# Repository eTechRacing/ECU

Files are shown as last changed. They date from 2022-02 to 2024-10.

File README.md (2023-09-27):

# SHIELD

ADCAN files moved to ADCAN-Legacy branch

_Pendent de publicar en angles

La shield ha de ser una placa versàtil i robusta que serveixi per implementar fàcilment elements comuns que comparteixen diverses plaques. L’avantatge d’implementar una shield és la de disposar d’una base coneguda, provada i fiable per, 
a partir d’ella, implementar qualsevol altre sistema que s’hagi d’incloure dins del cotxe.
Les funcionalitats de la placa shield passen, principalment, per una alimentació estable i constant i per un bus de comunicacions amplament validat i funcional. 
Tot això rodejant d’un microcontrolador molt consistent encarregat de l’adquisició, el processament i l’enviament de dades.

Requisits:
-Alimentació a 5 V i 3.3 V a partir de LV
-Comunicació via CAN1 i CAN2
-Connectors plug-and-play
-MCU potent (STM23)
-Documentació
-Reduir EMIs i soroll amb un bon disseny

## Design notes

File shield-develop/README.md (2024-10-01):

# SHIELD

ADCAN files moved to ADCAN-Legacy branch

_Pendent de publicar en angles

La shield ha de ser una placa versàtil i robusta que serveixi per implementar fàcilment elements comuns que comparteixen diverses plaques. L’avantatge d’implementar una shield és la de disposar d’una base coneguda, provada i fiable per, 
a partir d’ella, implementar qualsevol altre sistema que s’hagi d’incloure dins del cotxe.
Les funcionalitats de la placa shield passen, principalment, per una alimentació estable i constant i per un bus de comunicacions amplament validat i funcional. 
Tot això rodejant d’un microcontrolador molt consistent encarregat de l’adquisició, el processament i l’enviament de dades.

Requisits:
-Alimentació a 5 V i 3.3 V a partir de LV
-Comunicació via CAN1 i CAN2
-Connectors plug-and-play
-MCU potent (STM23)
-Documentació
-Reduir EMIs i soroll amb un bon disseny

El conntector entre la shield i la carrier és una de les parts fonamentals de la placa. La idea és que hi hagi connexió electrica i mecànica entre elles.
S'opta per un connector board-to-board tipus pin header (fabricant Würth) ja que dona la opció d'encaixar una placa sobre l'altre i, a mes, de disposar de totes les connexions
amb un connector senzill de posar i treure.

El microcontrolador és el més potent que s'ha pogut aconseguir per patrocinadors. Més concretament el STM32F777VI6T que compleix de sobres tots els requisits. De totes maneres,
pensant en el fet de que la shield sigui una placa amb futur, s'afageix una memoria EEPROM utilitzat el I2C número 4 del STM32.

Pel que fa la resta de la placa no hi ha cap complicació. S'implementa un USB_OTG amb un connector micro USB 2.0 per debug i visualització de dades per PC. Es fa servir el CAN
transceiver MCP2551 de microchip (fàcil d'aconseguir per samples) i unes proteccions i filtres a la linea CAN bastant estàndard. La resta dels pins del MCU van directament al
pin header excepte:
-VBAT: es col·loca un divisor de tensió rebaixant 30V a 3.3V. Això permet fer servir VBAT com una entrada analogica per medir la tensió que ofereix la LV.
-VBUS: es fa servir com a entrada digital per detectar si hi ha presencia d'USB.
-NRST: pin de reset del micocontrolador. Necessari per programar. Se li posa un botó per també poder fer reset manualment.
-Boot0: se li posa un switch per curtcircuitar a 3.3V o a GND. Això permetrà setejar al micro com a blank i poder carregar informació des del USB o programar més facilment.

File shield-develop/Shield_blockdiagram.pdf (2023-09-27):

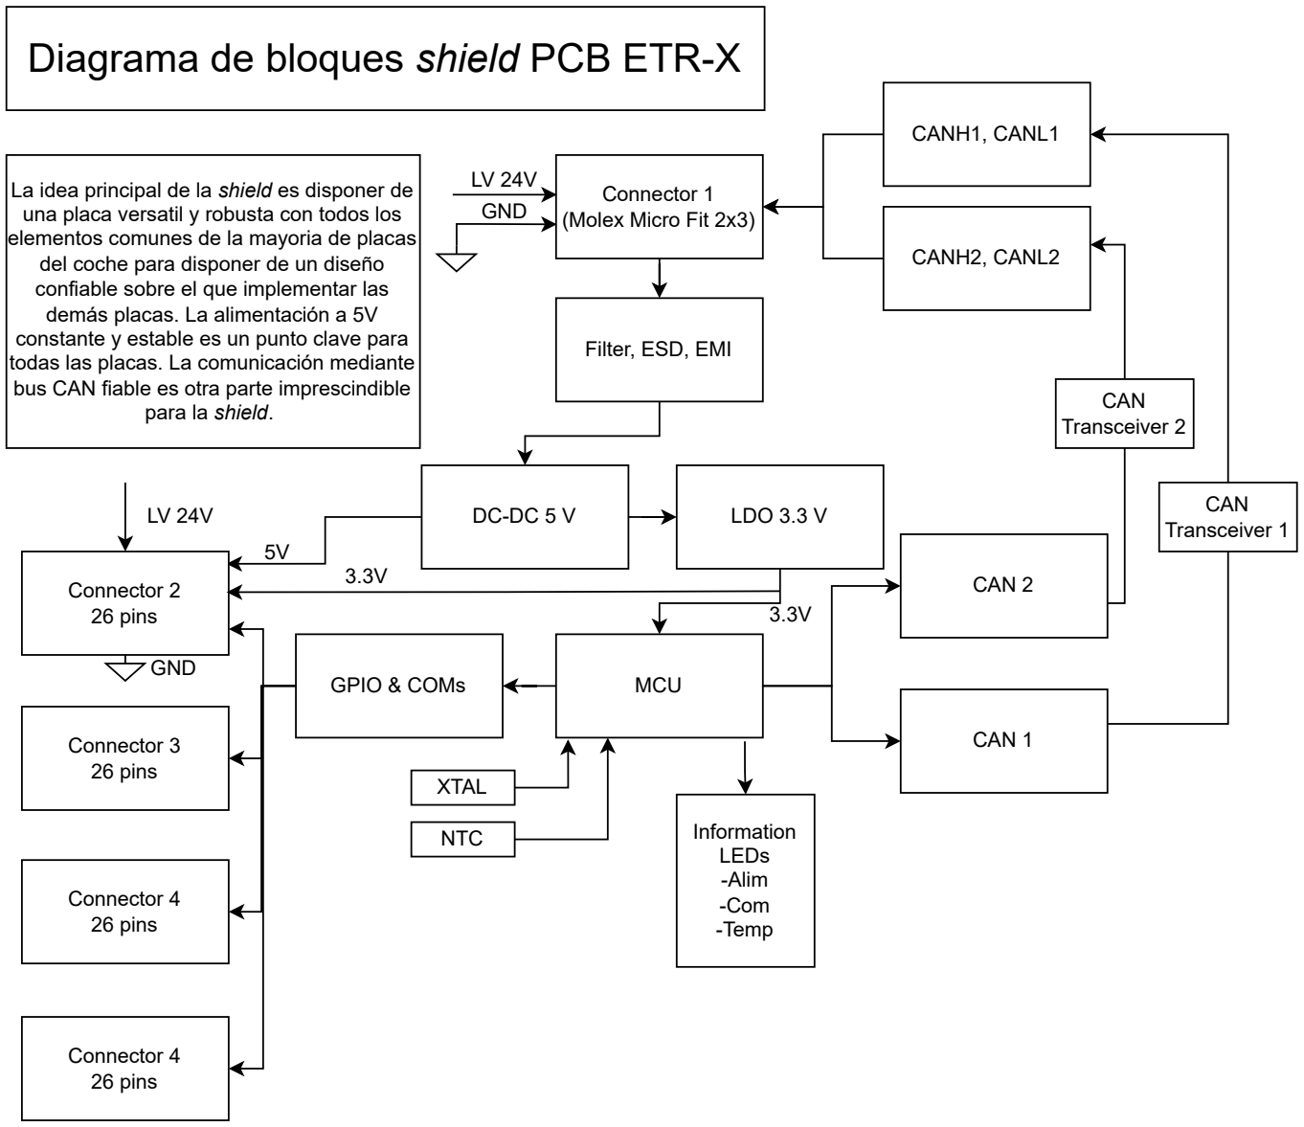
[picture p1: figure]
Connector 1 (Molex Micro Fit 2x3); Filter, ESD, EMI; MCU; CAN 2; GPIO & COMs; CAN 1; CANH1, CANL1; CANH2, CANL2; Connector 2 26 pins; XTAL; del coche para disponer de un diseño confiable sobre el que implementar las demás placas. La alimentación a 5V; para la shield.; Information LEDs -Alim -Com -Temp; Diagrama de bloques shield PCB ETR-X; GND; Connector 3 26 pins; CAN Transceiver 2; CAN Transceiver 1; NTC; LDO 3.3 V; Connector 4 26 pins

La idea principal de la shield es disponer de una placa versatil y robusta con todos los elementos comunes de la mayoria de placas

constante y estable es un punto clave para todas las placas. La comunicación mediante bus CAN fiable es otra parte imprescindible

PROVISIONAL BOM
-Molex Nano Fit 2x3
-Pin headers x4
-EMI filter
-ESD
-Alim Filter
-DC-DC 24V-5 V
-LDO 3.3 V
-STM32
-XTAL >120MHz
-SMD LEDs
-CAN Transceiver (x2)
-SMD NTC

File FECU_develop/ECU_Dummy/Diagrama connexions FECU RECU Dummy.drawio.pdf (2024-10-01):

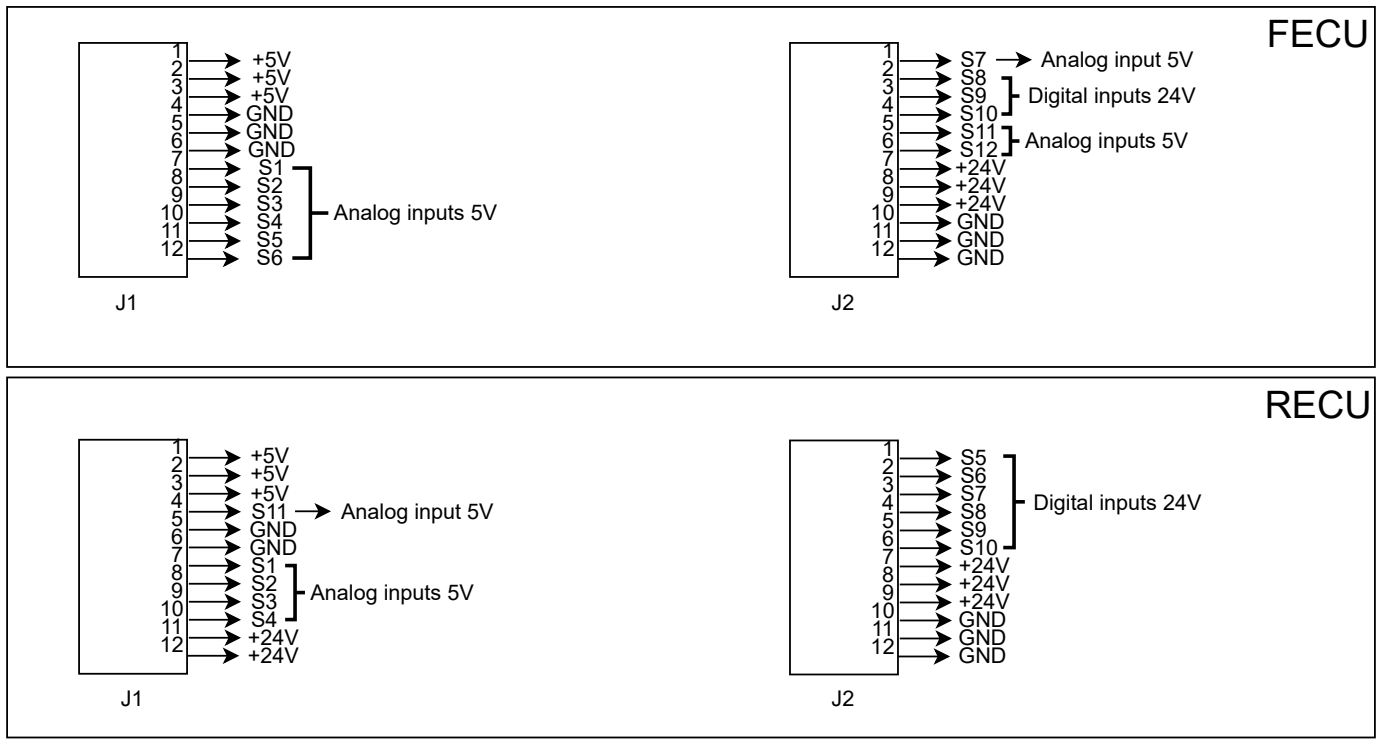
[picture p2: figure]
FECU; RECU; +5V +5V +5V GND GND GND S1 S2 S3 S4 S5 S6; Analog inputs 5V; S7 S8 S9 S10 S11 S12 +24V +24V +24V GND GND GND; Digital inputs 24V; S5 S6 S7 S8 S9 S10 +24V +24V +24V GND GND GND; +5V +5V +5V S11 GND GND S1 S2 S3 S4 +24V +24V; Analog input 5V
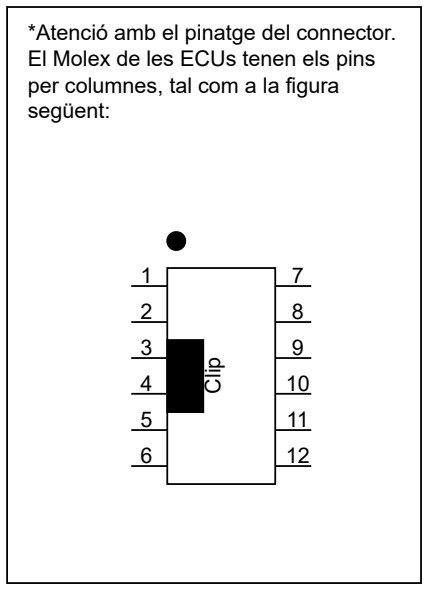
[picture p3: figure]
*Atenció amb el pinatge del connector. El Molex de les ECUs tenen els pins per columnes, tal com a la figura següent:; Clip

Taula connexions connectors des de les ECUs a ECU Dummy:

FRONT ECU

-J1 va a JFS1
-J2 va a JFRS2

REAR ECU

-J1 va a JRS1
-J2 va a JFRS2

*El connector JFRS2 es compatible amb el J2 de les dos ECUs. Nomes n'hi ha un a la ECU_Dummy per tant només es pot fer test del J2 a una ECU alhora

# ECUs & ECU_Dummy interconnections

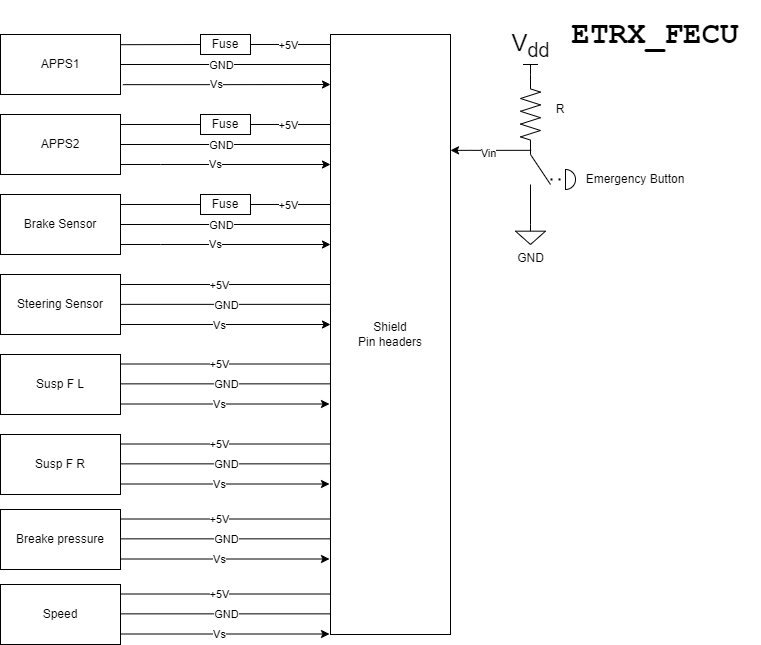
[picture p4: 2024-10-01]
FECU_develop/ETRX_FECU/ETRX_FECU_FlowDiagram.drawio.png

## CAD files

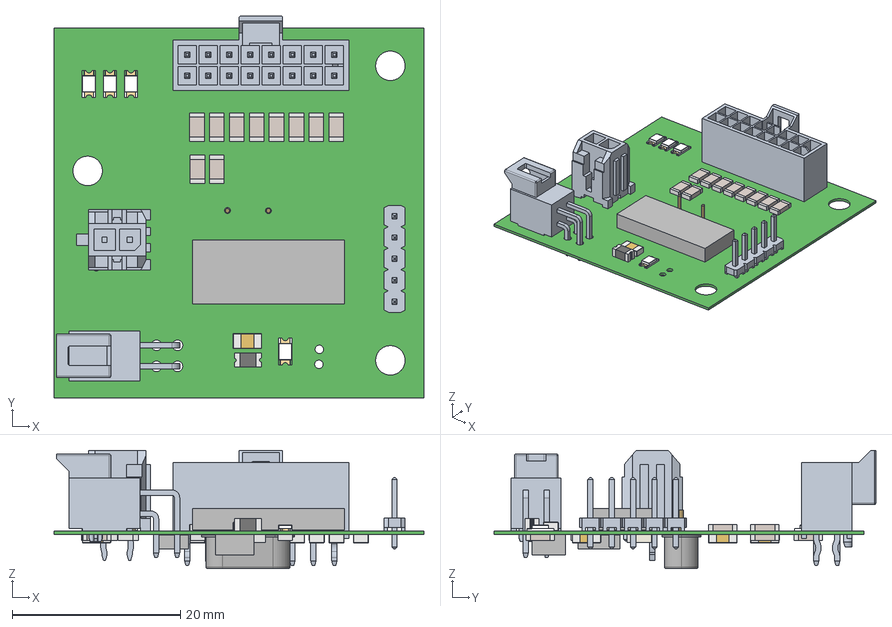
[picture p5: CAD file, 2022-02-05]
cleanup-functions/ADCAN/ADCAN_PCB/ADCAN_V3.step
44.0 x 45.4 x 14.1 mm
MTLW-105-05-X-S-190
Open_CASCADE_STEP_translator_6.8_13.1.1 x 11
Open_CASCADE_STEP_translator_6.8_13.1.2 x 11
Open_CASCADE_STEP_translator_6.8_13.2.1 x 11
Extruded x 84
housing x 4
marking x 8
cover x 4
base x 8
Crystal_HC49-4H_Vertical

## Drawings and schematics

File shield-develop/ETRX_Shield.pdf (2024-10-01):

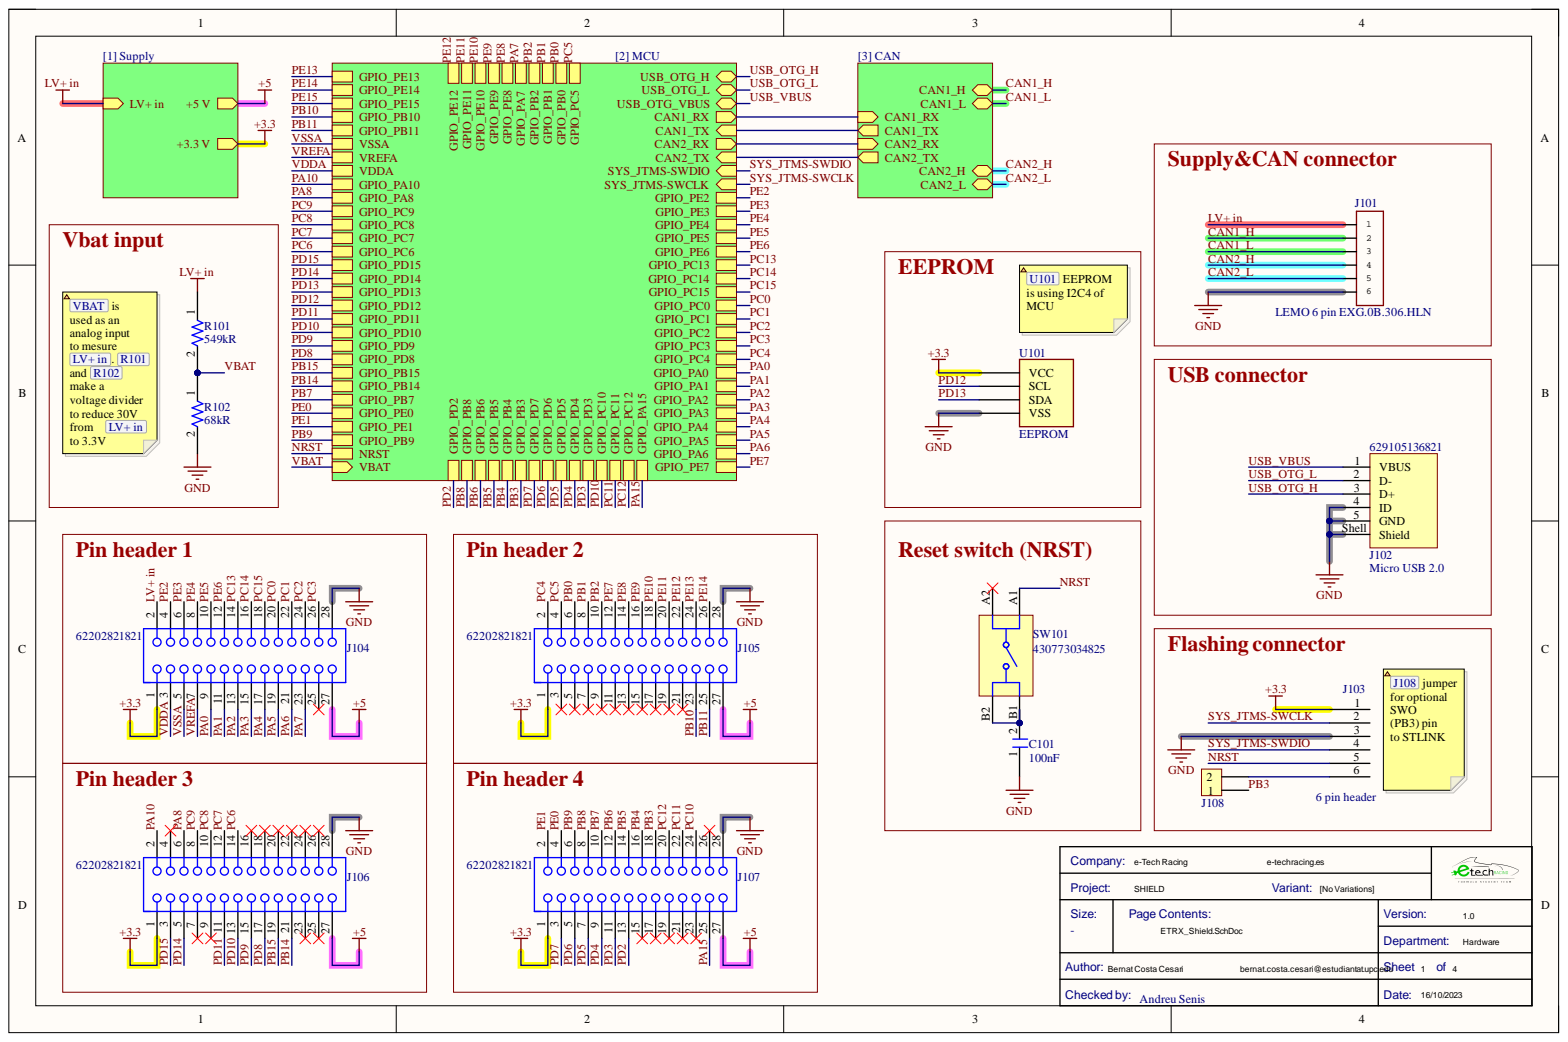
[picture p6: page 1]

LEMO 6 pin EXG.0B.306.HLN

Author: BernatCosta Cesari bernat.costa.cesari@estudiantat.upc.edu | Sheet 1 of 4

Checked by: Andreu Senis | Date: 16/10/2023

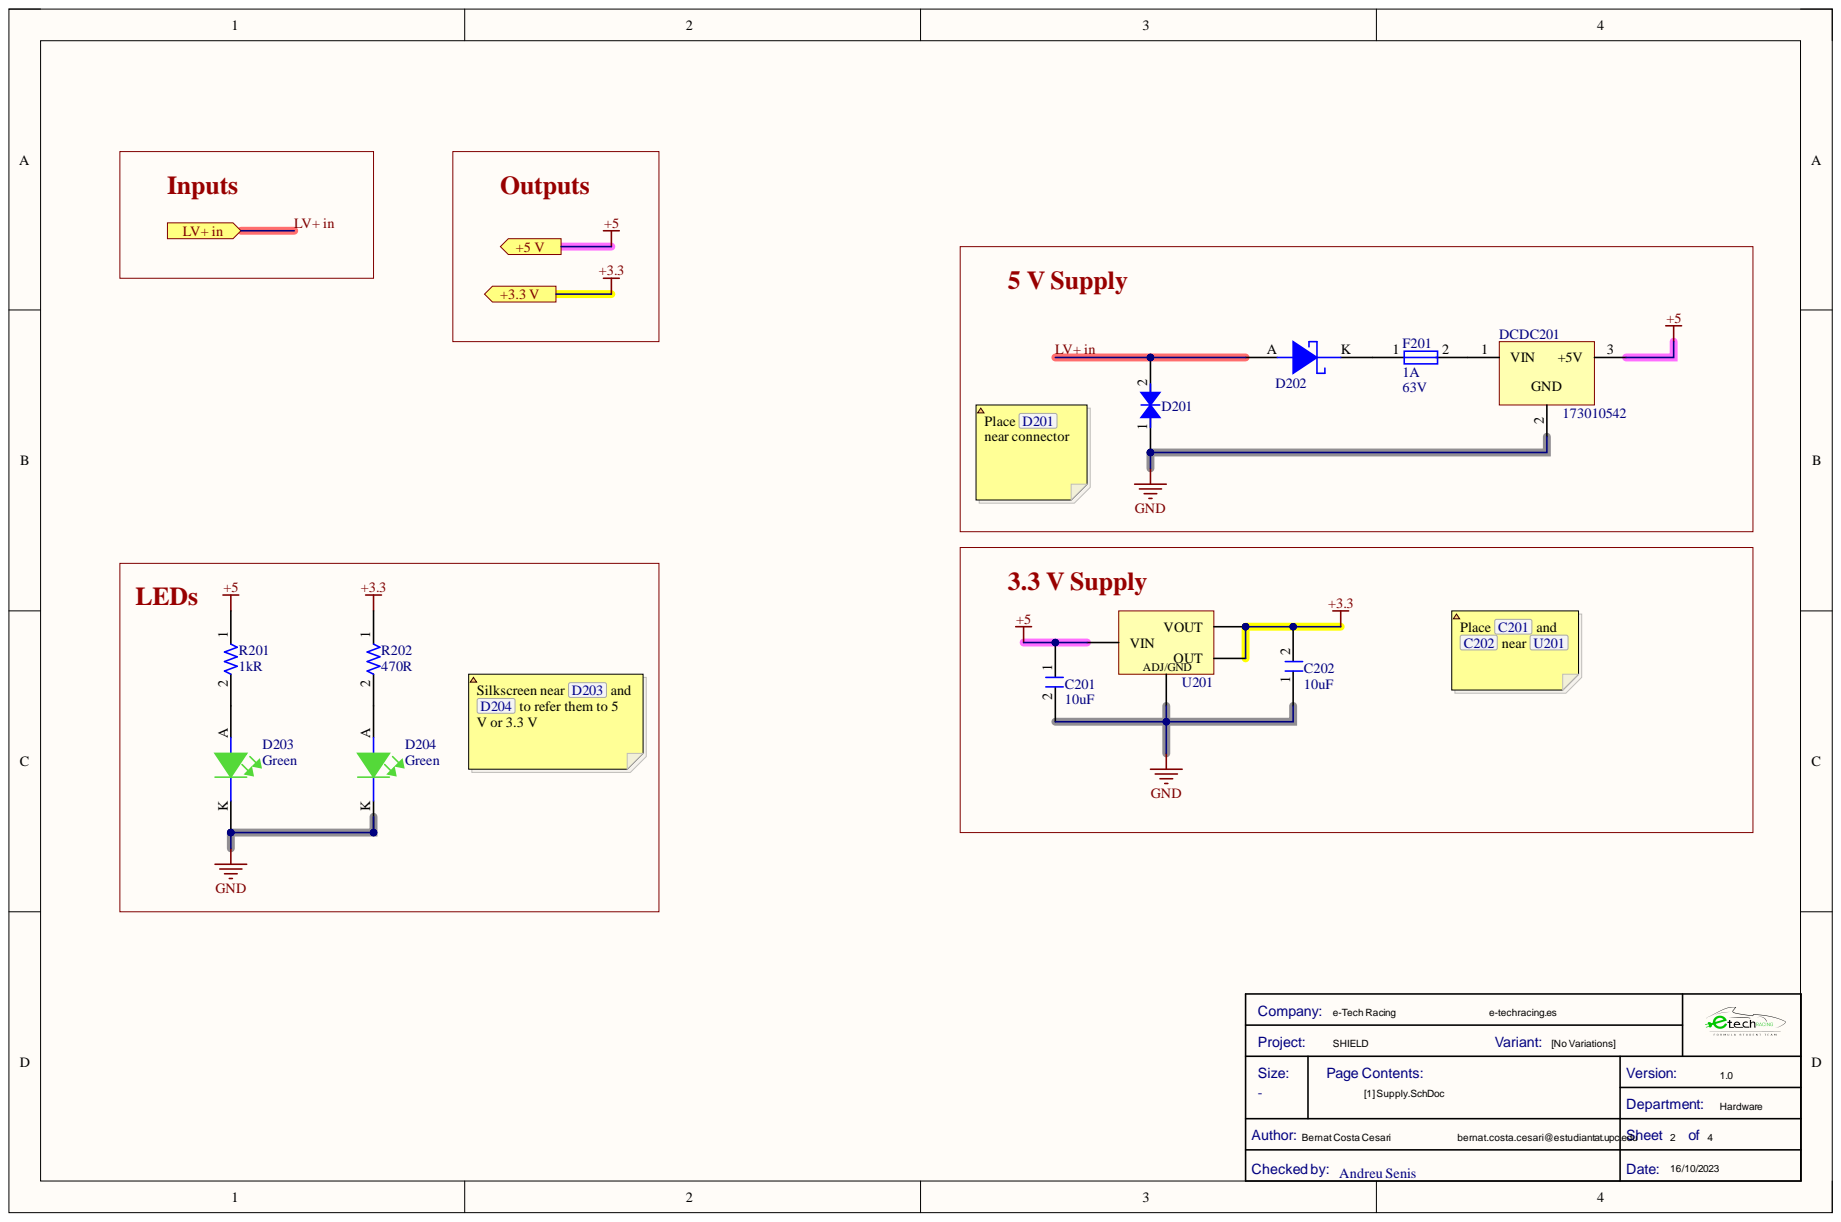
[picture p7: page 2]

Silkscreen near D203 and
D204 to refer them to 5

bernat.costa.cesari@estudiantat.upc.edu

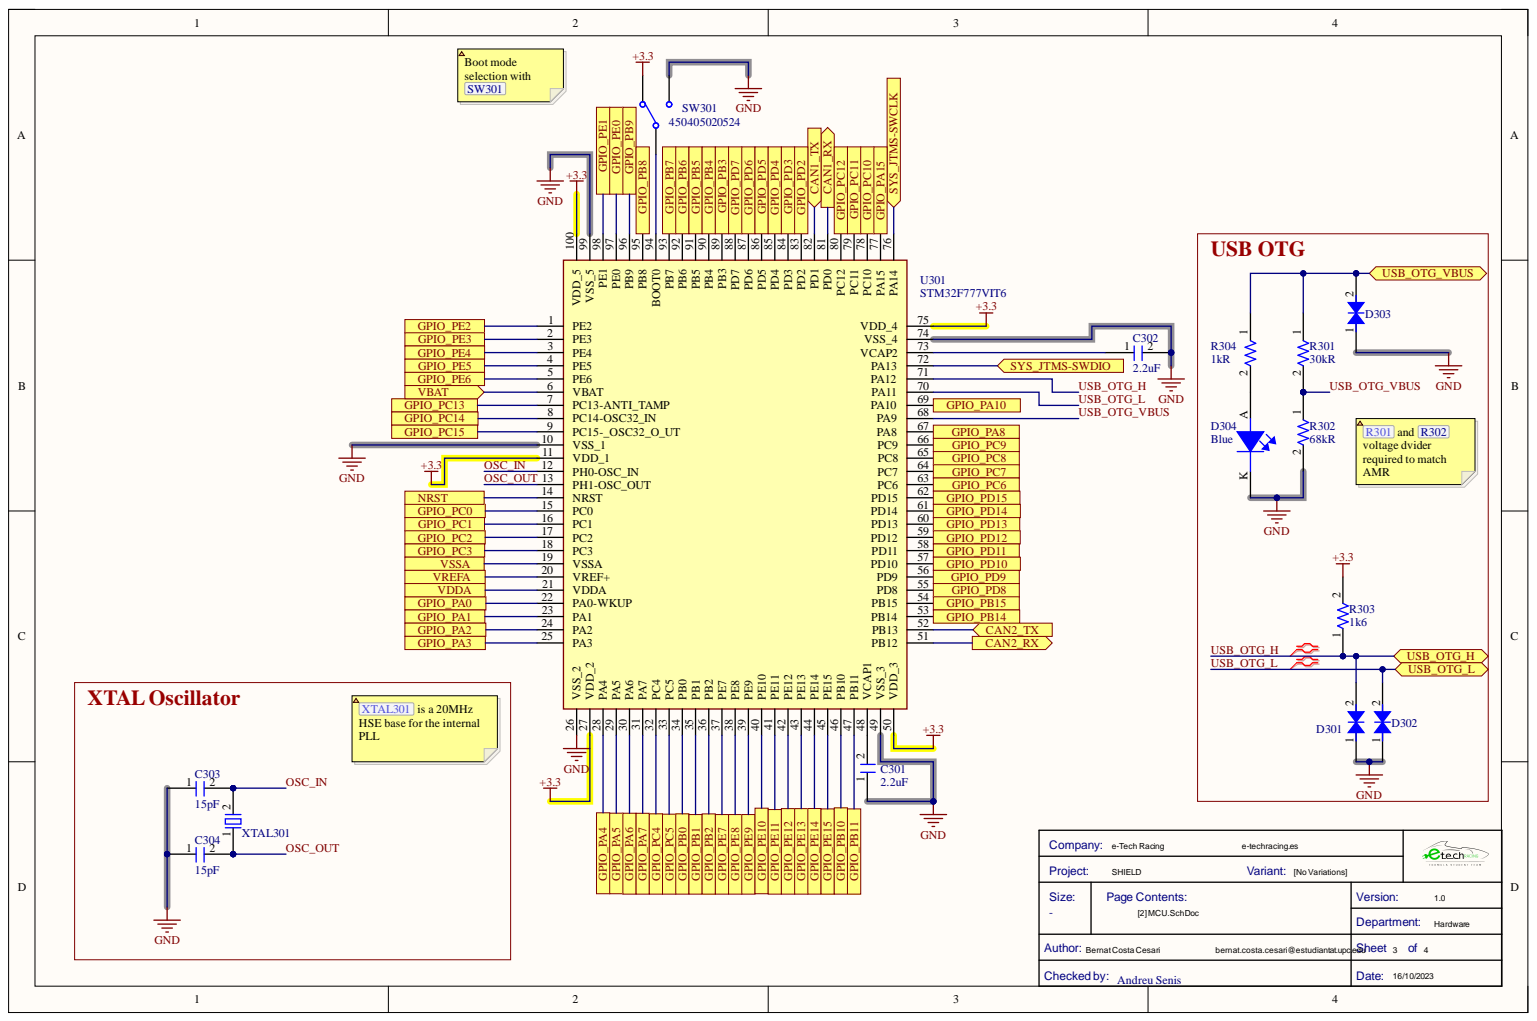
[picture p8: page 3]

GPIO_PC15 | | GPIO_PA8

VDD_1 11

OSC_IN | PH0-OSC_IN 12

GPIO_PC3 | GPIO_PD11
VSSA | GPIO_PD10

XTALOscillator | XTAL301 is a 20MHz HSE base for the internal PLL C303

Author: BernatCosta Cesari bernat.costa.cesari@estudiantat.upc.edu | Sheet 3 of 4

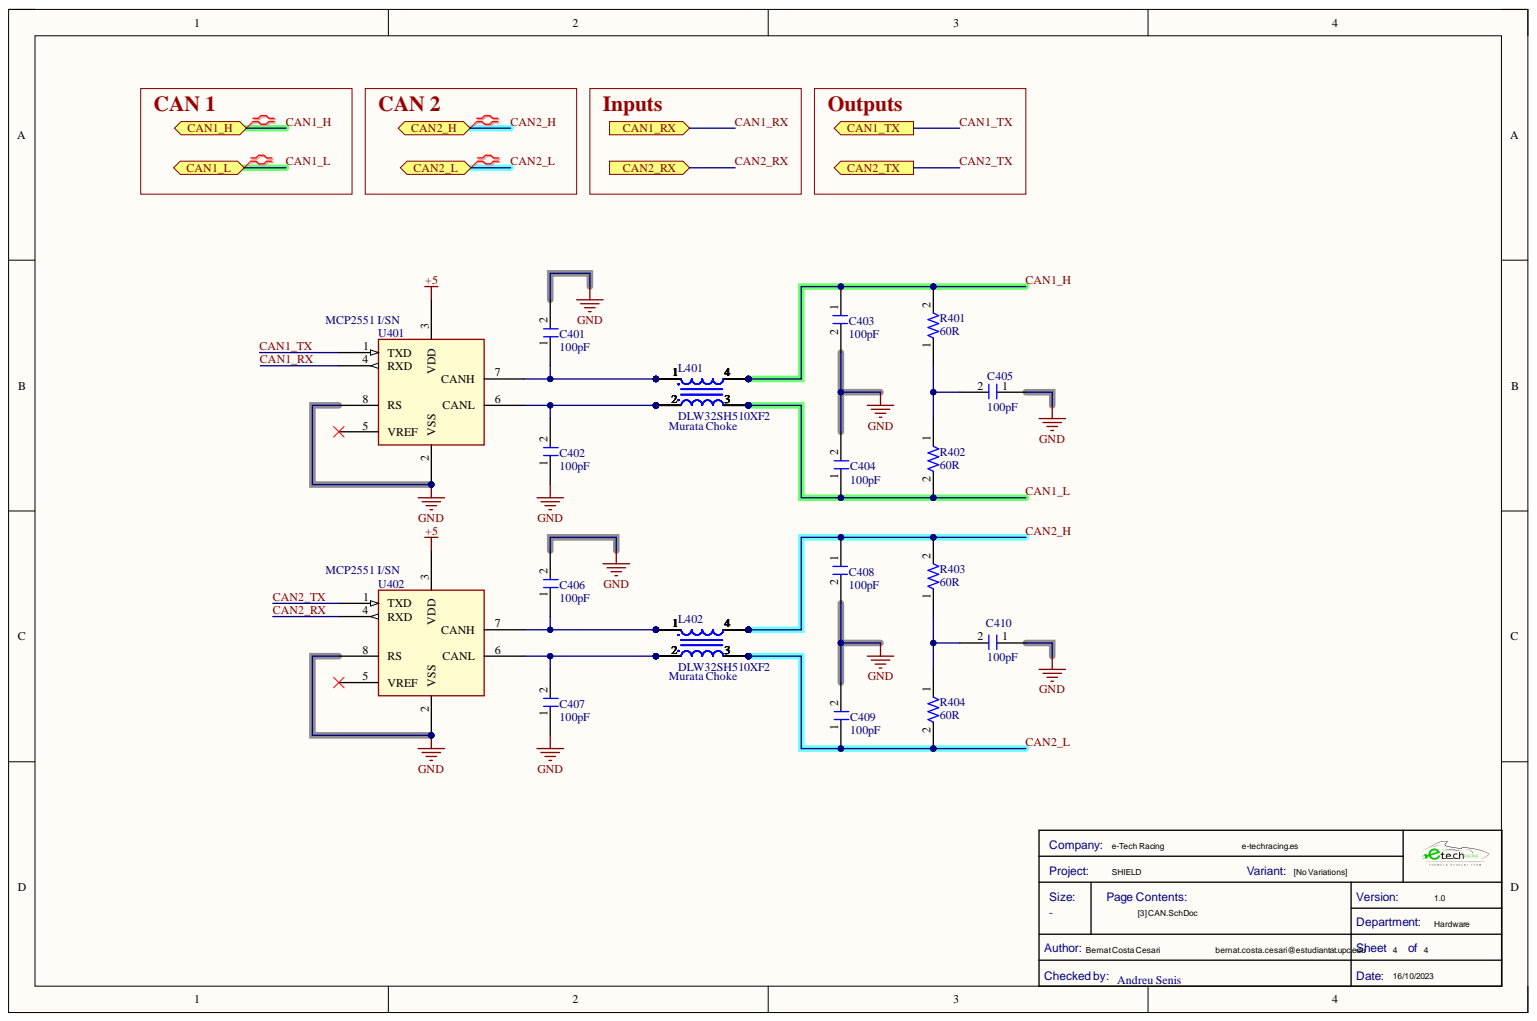
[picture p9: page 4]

bernat.costa.cesari@estudiantat.upc.edu

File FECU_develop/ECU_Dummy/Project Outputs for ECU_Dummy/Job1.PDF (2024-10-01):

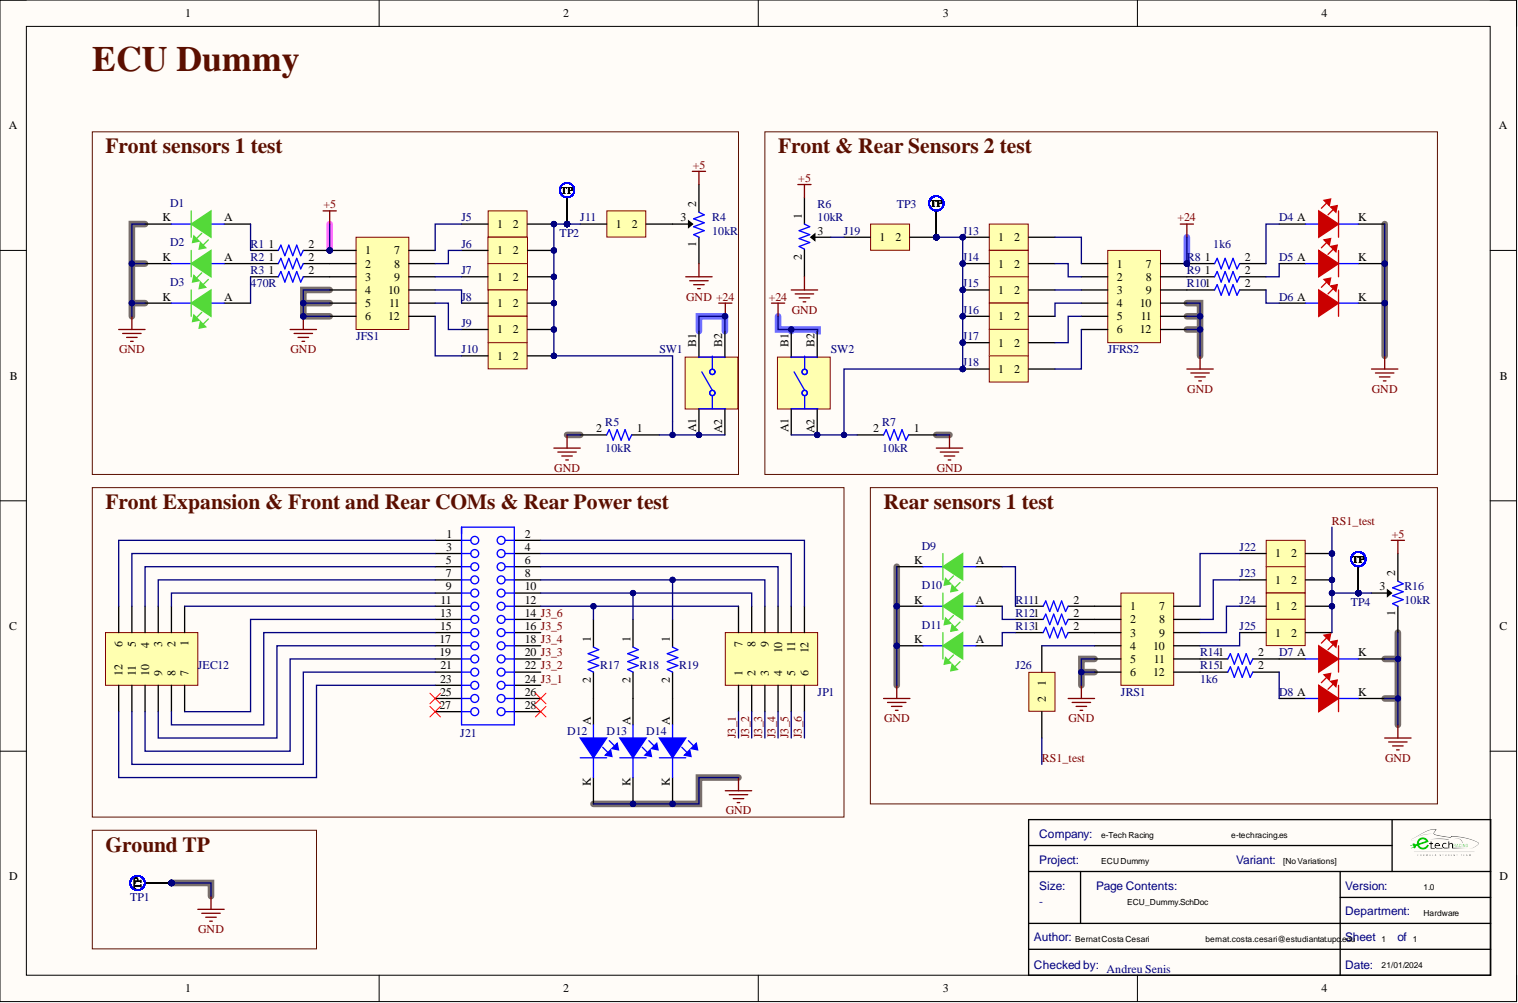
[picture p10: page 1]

Front & Rear Sensors 2 test

Front Expansion & Front and Rear COMs & Rear Power test

Author: BernatCosta Cesari bernat.costa.cesari@estudiantat.upc.edu | Sheet 1 of 1

Checked by: Andreu Senis | Date: 21/01/2024

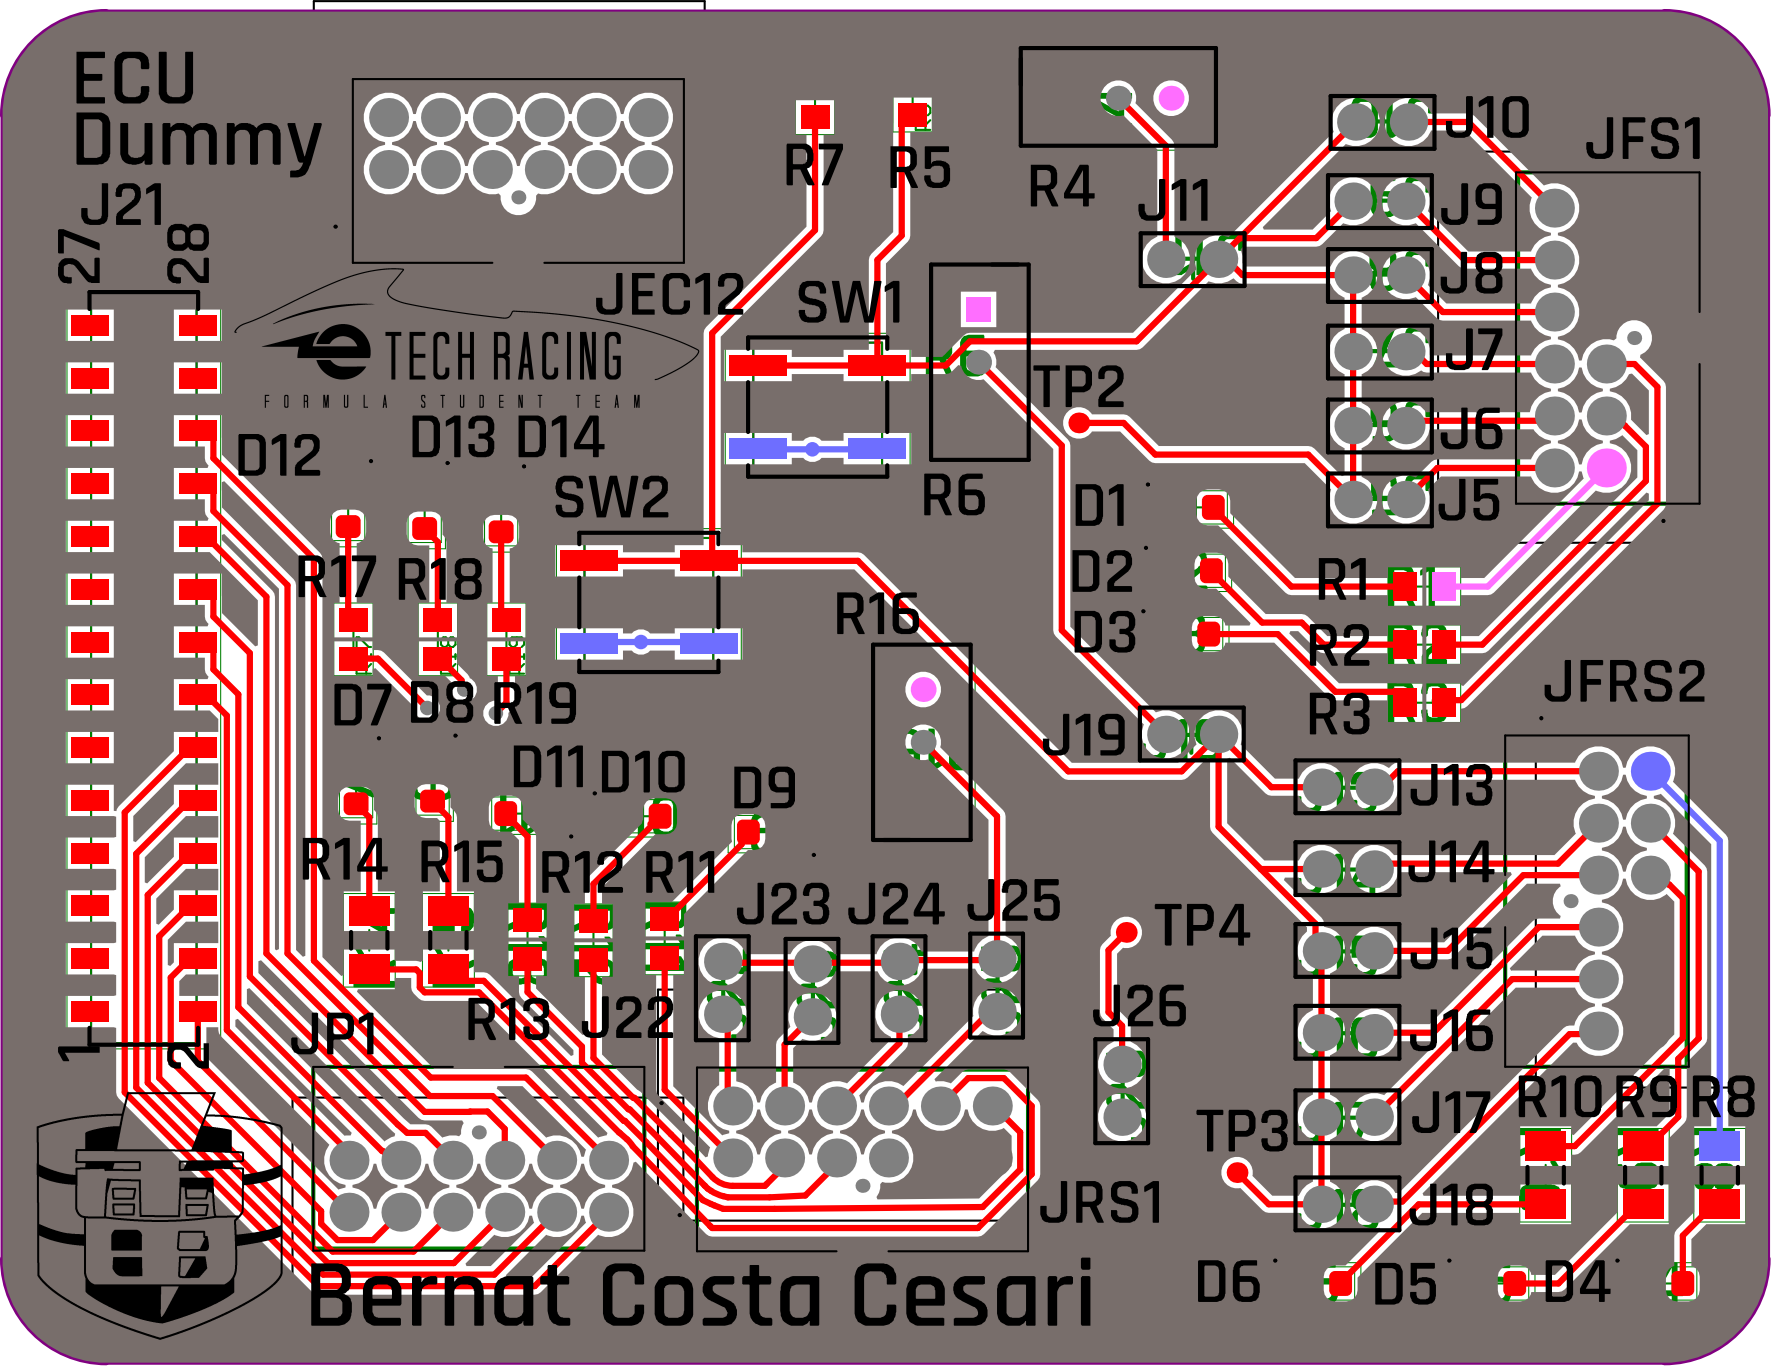
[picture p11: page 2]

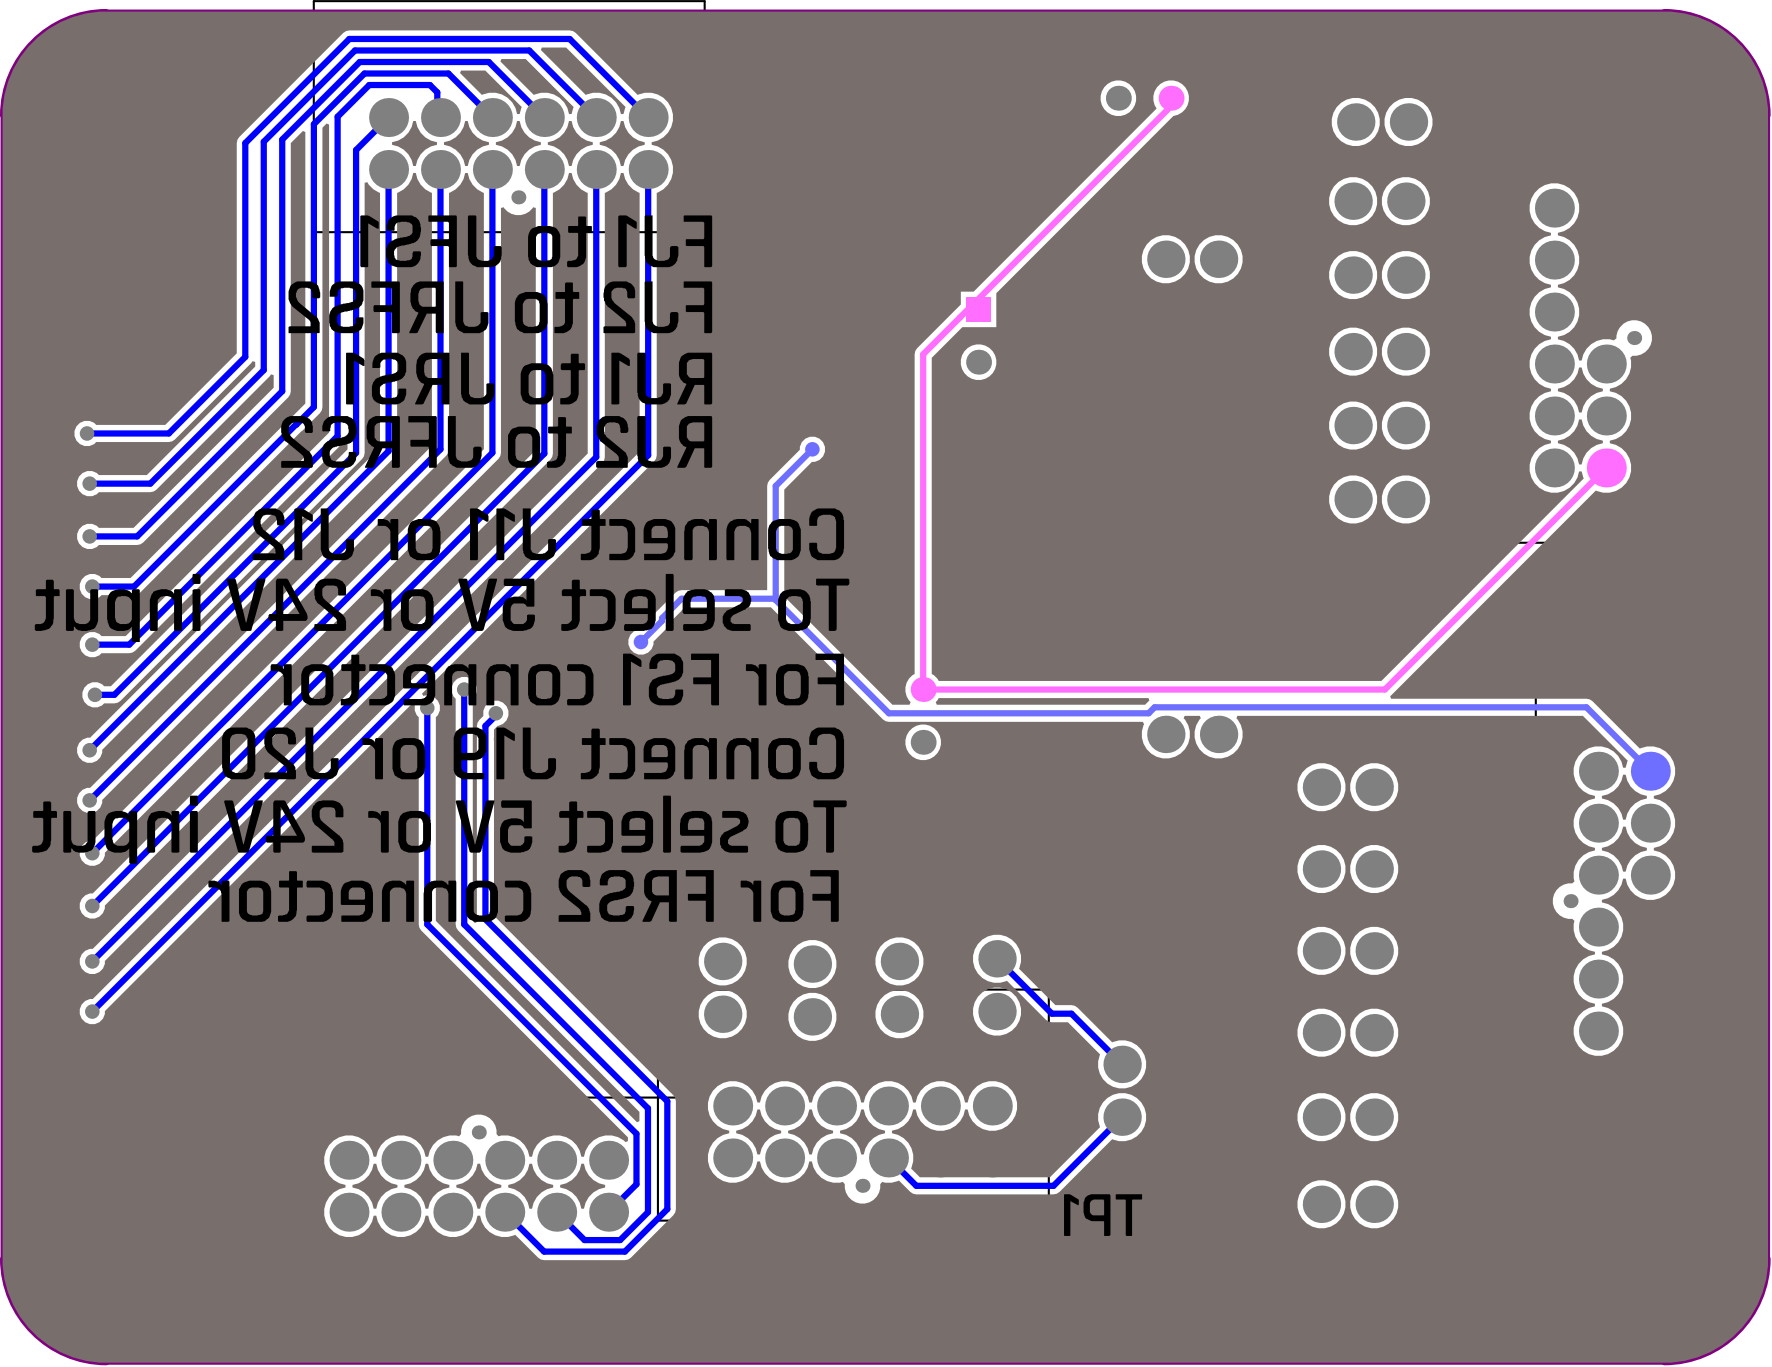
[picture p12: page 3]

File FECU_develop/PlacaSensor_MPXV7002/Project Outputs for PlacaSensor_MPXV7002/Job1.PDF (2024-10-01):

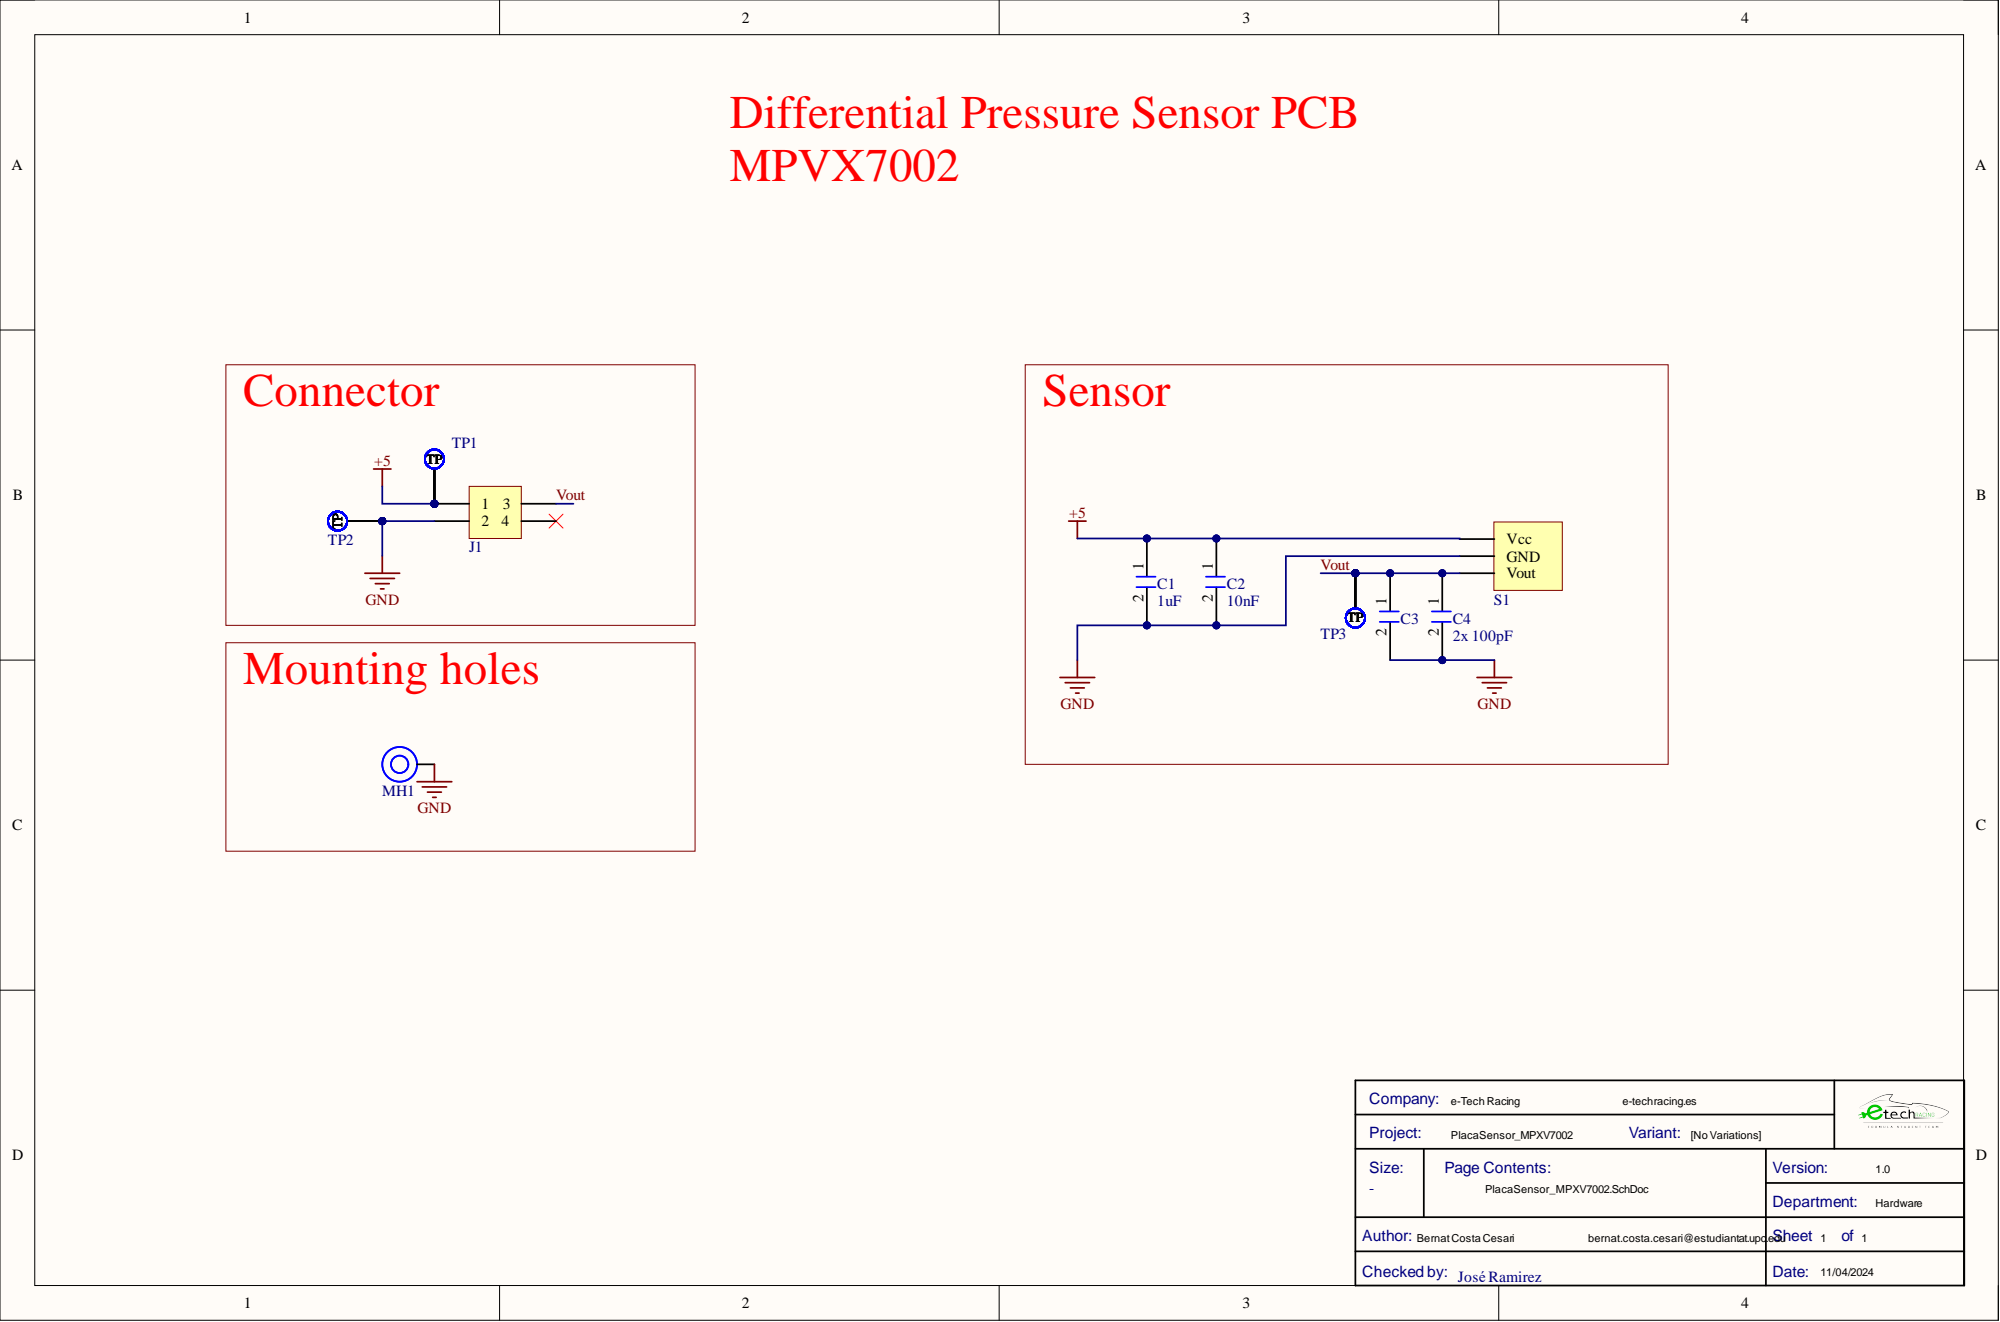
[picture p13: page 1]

Differential Pressure Sensor PCB
MPVX7002

Mounting holes GND TP TP1

Author : B e r n a t C o s t a C e s a ri b e r n a t . c o s t a . c e s a r i @ e s t u d i a n ta t . u p c | . e Shee d u t 1 o f 1

Chec ked by : J o s é Ramirez | Dat e : 1 1 / 0 4 /2 0 2 4

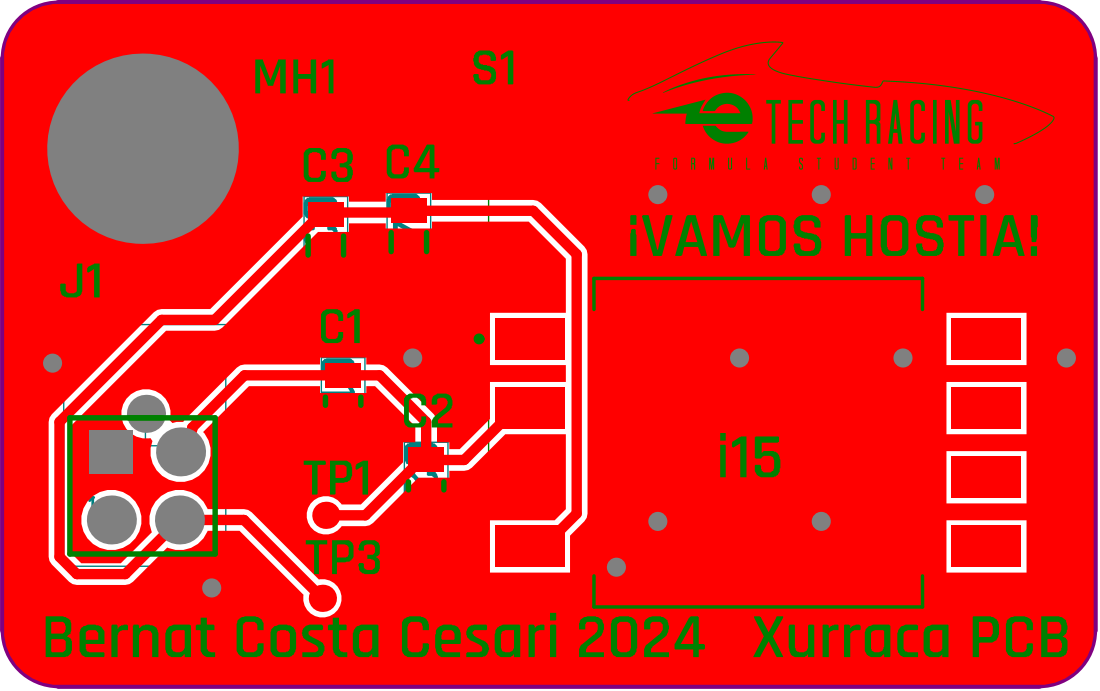
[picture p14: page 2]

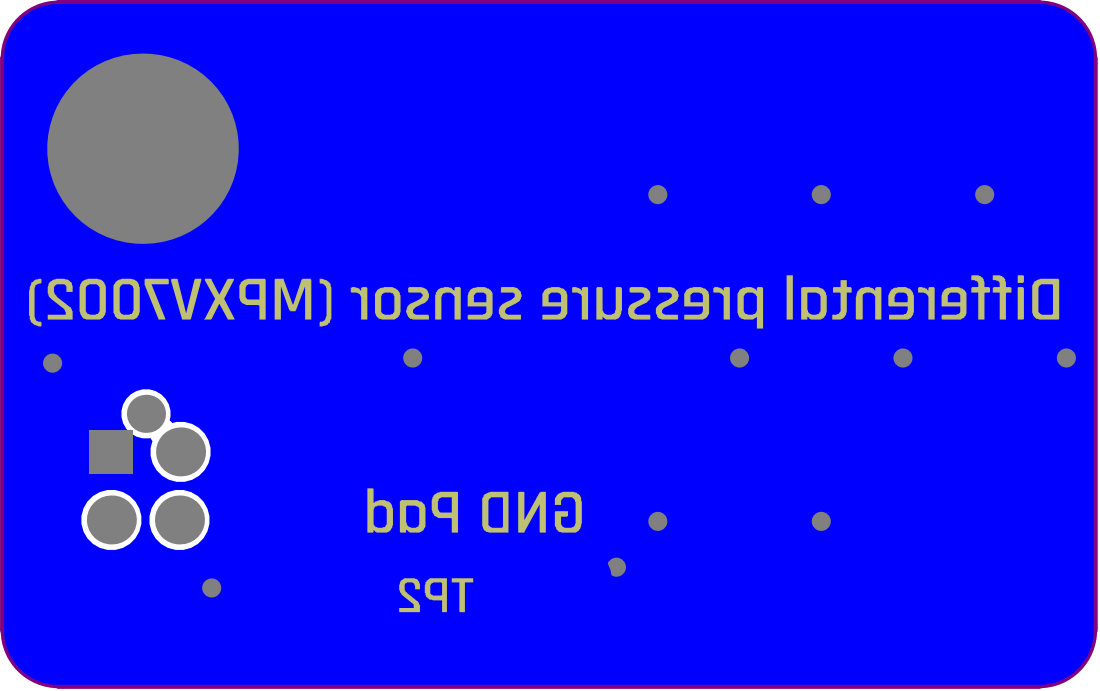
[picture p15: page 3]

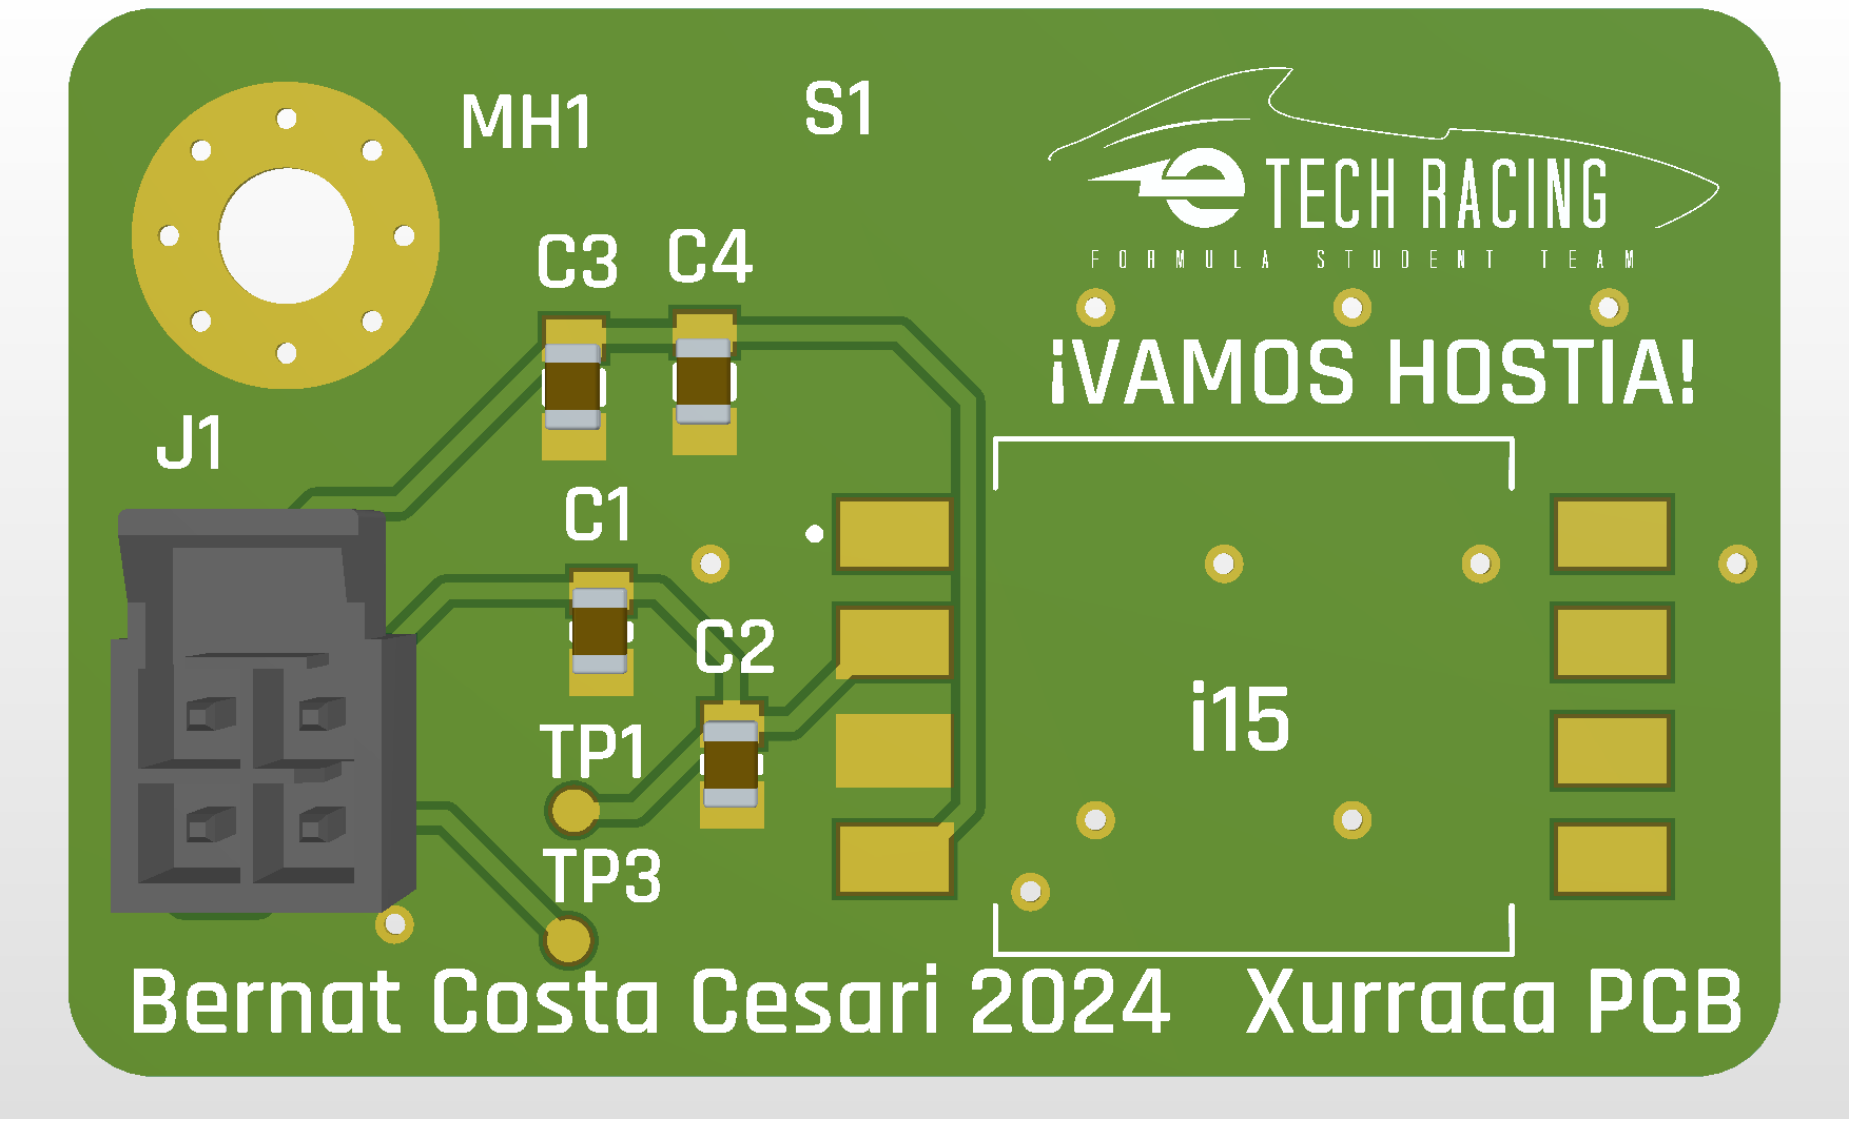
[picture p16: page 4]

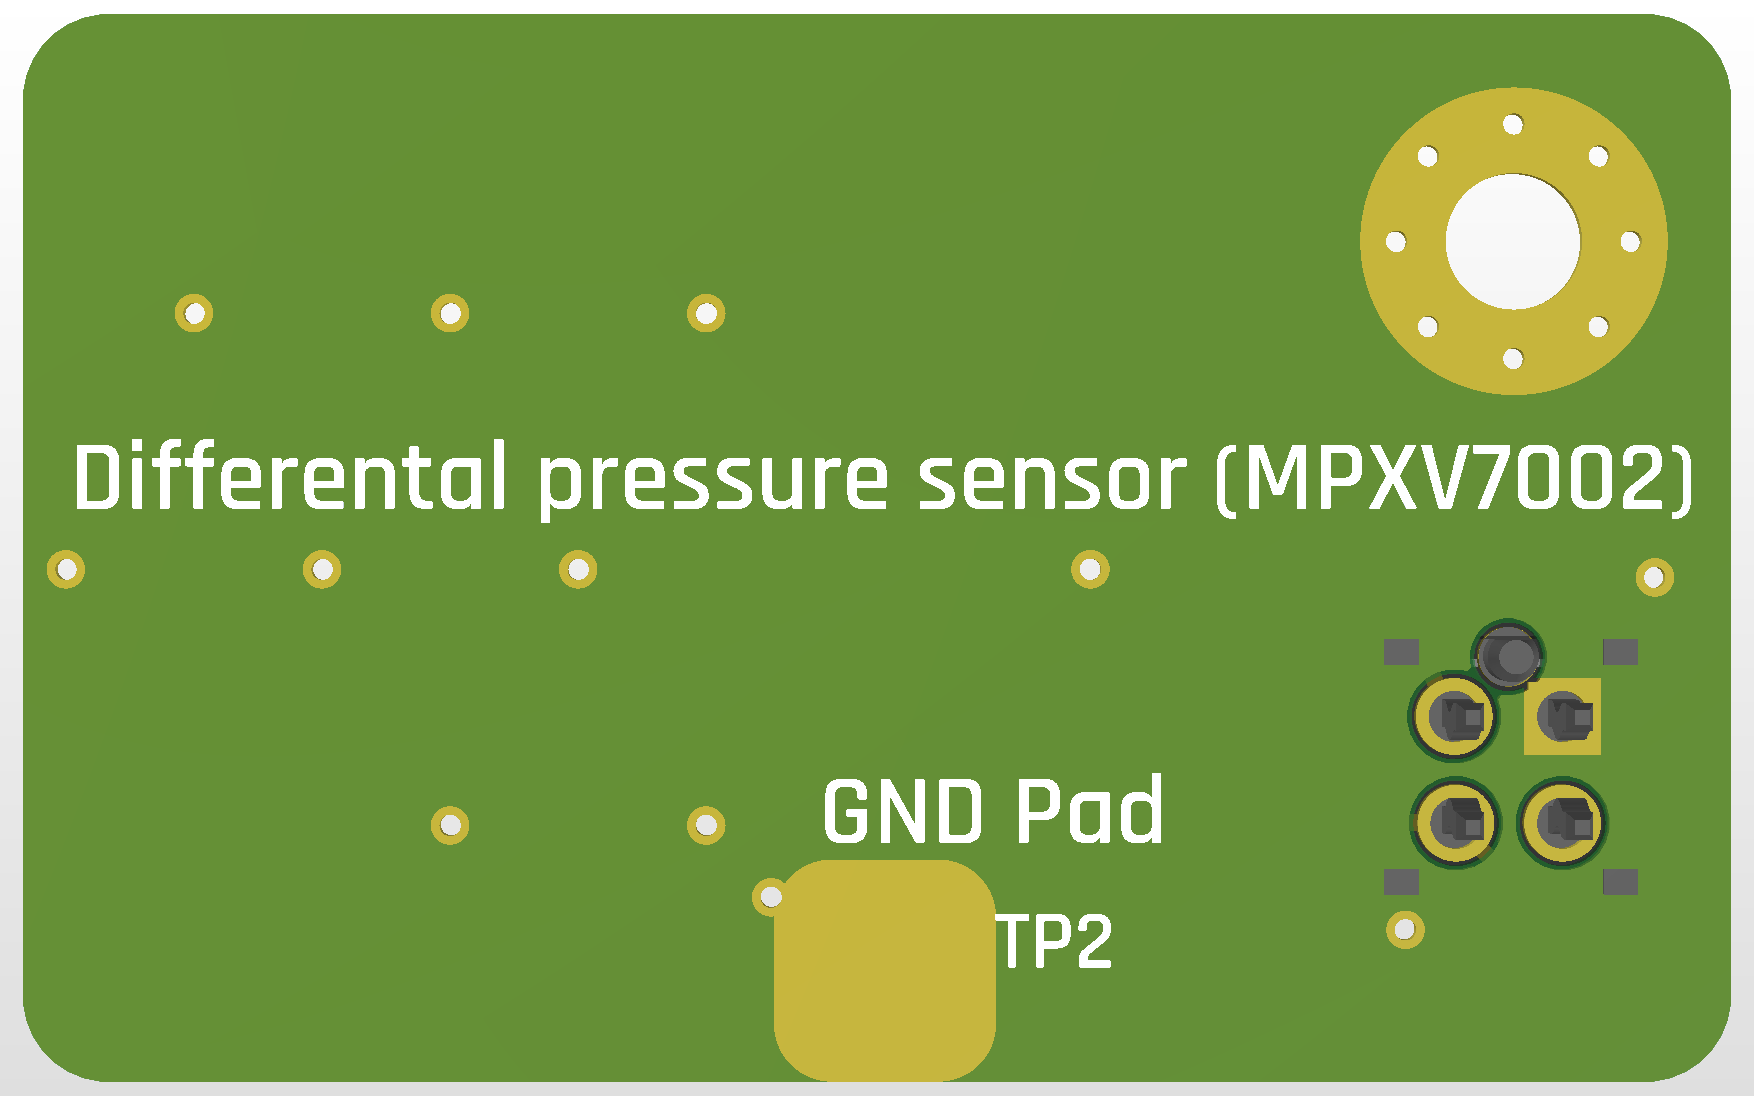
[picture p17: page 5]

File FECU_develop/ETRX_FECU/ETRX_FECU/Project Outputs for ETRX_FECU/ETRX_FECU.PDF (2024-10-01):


F2 1 | 2
F3 1 | 2

Author : B e r n a t C o s t a e s a ri b e r n a t . c o s t a . c e s a r i @ e s t u d i a n ta t . u p | c . e Shee d u t 1 o f 5

Chec ked by : A n dreu Sen i s | Dat e : 3 1 / 0 3 /2 0 2 4


Author : e r n a t o s t a e s a ri b e r n a t . c o s t a . c e s a r i @ e s t u d i a n ta t . u p | c . e Shee d u t 2 o f 5

Chec ked by : n dreu Sen i s | Dat e : 3 1 / 0 3 /2 0 2 4


Author : e r n a t o s t a e s a ri b e r n a t . c o s t a . c e s a r i @ e s t u d i a n ta t . u p | c . e Shee d u t 3 o f 5

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



Line # | Designator | Name | Quantity

C208, C209, C210 | 885012207098 | 3
F1, F2, F3, F4, F5, F6 | 0437001.WRA | 6
J1, J2, J3, J4 | 1053101112 | 4
MH1, MH2, MH3, MH4 | Mounting_Hole_M3 | 4
MH5, MH6, MH7, MH8 | Mounting_Hole_M4 | 4
R1, R2, R3, R4 | CR0805-JW-103ELF | 4
R201, R203, R205, R207, R209, R211, R213, R221, R223 | CR0805-JW-102ELF | 9

R215, R217, R219 | 12k5 | 3
R216, R218, R220 | 2k | 3
U101 | ETR_SHIELD_III | 1

Surface Material Bottom Solder 0.01mm Solder Resist Solder Mask GBS




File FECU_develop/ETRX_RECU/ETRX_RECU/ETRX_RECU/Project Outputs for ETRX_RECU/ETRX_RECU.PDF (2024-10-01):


F2 1 | 2
F3 1 | 2

Author: BernatCosta Cesari bernat.costa.cesari@estudiantat.upc.edu | Sheet 1 of 4

Checked by: Andreu Senis | Date: 08/04/2024


Author : B e r n a t C o s t a e s a ri b e r n a t . c o s t a . c e s a r i @ e s t u d i a n ta t . u p c | . e Shee d u t o f

Chec ked by : A n dreu Sen i s | Dat e : /


Author : e r n a t o s t a e s a ri b e r n a t . c o s t a . c e s a r i @ e s t u d i a n ta t . u p c | . e Shee d u t o f

Chec ked by : n dreu Sen i s | Dat e : /

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

Chec ked by : n dreu Sen i s | Dat e : /








Line # | Designator | Name | Quantity

F1, F2, F3, F4, F5, F6, F7, F8 | 0437001.WRA | 8

J1, J2, J3, J4 | 1053101112 | 4
MH1, MH2, MH3, MH4 | Mounting_Hole_M3 | 4
MH5, MH6, MH7, MH8 | Mounting_Hole_M4 | 4
Q301, Q302, Q303 | CPH3455-TL-H | 3
R101, R102, R301, R302, R303, R304, R305, R306 | CR0805-JW-103ELF | 8

R201, R203, R205, R207, R221, R307, R309 | CR0805-JW-102ELF | 7

U1 | ETR_SHIELD_III | 1

Surface Material Bottom Solder 0.01mm Solder Resist Solder Mask GBS

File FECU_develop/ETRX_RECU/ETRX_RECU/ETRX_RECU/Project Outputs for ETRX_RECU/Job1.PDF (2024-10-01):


F2 1 | 2
F3 1 | 2

Author: BernatCosta Cesari bernat.costa.cesari@estudiantat.upc.edu | Sheet 1 of 4

Checked by: Andreu Senis | Date: 11/06/2024


Author : B e r n a t C o s t a e s a ri b e r n a t . c o s t a . c e s a r i @ e s t u d i a n ta t . u p c | . e Shee d u t o f

Chec ked by : A n dreu Sen i s | Dat e : /


Author : e r n a t o s t a e s a ri b e r n a t . c o s t a . c e s a r i @ e s t u d i a n ta t . u p c | . e Shee d u t o f

Chec ked by : n dreu Sen i s | Dat e : /

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

Chec ked by : n dreu Sen i s | Dat e : /








Line # | Designator | Name | Quantity

F1, F2, F3, F4, F5, F6, F7, F8 | 0437001.WRA | 8

J1, J2, J3, J4 | 1053101112 | 4
MH1, MH2, MH3, MH4 | Mounting_Hole_M3 | 4
MH5, MH6, MH7, MH8 | Mounting_Hole_M4 | 4
Q301, Q302, Q303 | CPH3455-TL-H | 3
R101, R102, R301, R302, R303, R304, R305, R306 | CR0805-JW-103ELF | 8

R201, R203, R205, R207, R221, R307, R309 | CR0805-JW-102ELF | 7

U1 | ETR_SHIELD_III | 1

Surface Material Bottom Solder 0.01mm Solder Resist Solder Mask GBS

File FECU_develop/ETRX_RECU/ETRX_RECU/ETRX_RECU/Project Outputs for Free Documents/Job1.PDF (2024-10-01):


F2 1 | 2
F3 1 | 2

Author: BernatCosta Cesari bernat.costa.cesari@estudiantat.upc.edu | Sheet 1 of 4

Checked by: Andreu Senis | Date: 21/12/2023








Line # | Designator | Comment | Quantity
1 | C201, C202, C203, C204, C211, C301, C302, C303, C304, C305 | 885012207103 | 10

3 | F1, F2, F3, F4, F5, F6, F7, F8 | 0437001.WRA | 8
4 | J1, J2, J3, J4 | 1053101112 | 4
5 | J101, J102, J103, J104 | 62332821021 | 4
6 | MH1, MH2, MH3, MH4 | Mounting_Hole_M3 | 4
7 | MH5, MH6, MH7, MH8 | Mounting_Hole_M4 | 4
8 | Q301, Q302, Q303 | BC817-25LT1G | 3
9 | R201, R203, R205, R207, R221, R301, R303, R305, R307, R309 | CR0805-JW-102ELF | 10

13 | R302, R304, R306 | CR0805-JW-103ELF | 3

Surface Material Bottom Solder 0.01mm Solder Resist Solder Mask GBS

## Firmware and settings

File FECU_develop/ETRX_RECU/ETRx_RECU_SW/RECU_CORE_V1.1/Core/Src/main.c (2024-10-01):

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
/* Includes ------------------------------------------------------------------*/
#include "main.h"

/* USER CODE BEGIN Includes */
#include "RECU.h"
#include "eTechRacingADC.h"
#include "eTechRacing_Filters.h"
#include "can_comunication.h"
#include "stdint.h"
#include "stdio.h"
#include "P_Controller.h"

//ADC MEASURES-----------------------------------------------------------------------------------------------
uint16_t adc_buffer[2];
uint16_t Susp_R_R[2];
uint16_t Susp_R_L[2];

/* USER CODE END Includes */

/* USER CODE BEGIN PD */
//CODE VARIABLES---------------------------------------------------------------------------------------------
uint8_t Refri_Accu = 0;
uint8_t Refri_Inverters = 0;
uint8_t Refri_Motors = 0;
uint8_t Brakelight;
int duty_inverters;
int duty_motors;
int duty_accu;
uint8_t TSMS;
uint8_t TS_Right;
uint8_t TS_Left;
uint8_t HV_Box;
uint8_t HVD;

//Temperature control------------------------------------------------------------------------------------------
float Temperature_Accu;
float Inverter_R_Temp;
float Inverter_L_Temp;
float Inverter_Highest_Temp;
float Motor_R_Temp;
float Motor_L_Temp;
float Motor_Highest_Temp;

uint8_t DC_accu  = 127;
uint8_t DC_inverters = 200;

uint8_t Keep_Alive = 0;

P_Controller *pc;

//CAN--------------------------------------------------------------------------------------------
CAN_RxHeaderTypeDef RxHeader;
CAN_TxHeaderTypeDef TxHeader;
CAN_FilterTypeDef canfil;
CAN_FilterTypeDef canfil2;
uint8_t RxData[30];
uint8_t TxData[30];

/* USER CODE END PD */

ADC_HandleTypeDef hadc1;
ADC_HandleTypeDef hadc2;
DMA_HandleTypeDef hdma_adc1;

CAN_HandleTypeDef hcan1;
CAN_HandleTypeDef hcan2;

TIM_HandleTypeDef htim1;
TIM_HandleTypeDef htim3;
TIM_HandleTypeDef htim4;
TIM_HandleTypeDef htim8;

void SystemClock_Config(void);
static void MPU_Config(void);
static void MX_GPIO_Init(void);
static void MX_DMA_Init(void);
static void MX_ADC1_Init(void);
static void MX_CAN1_Init(void);
static void MX_CAN2_Init(void);
static void MX_TIM3_Init(void);
static void MX_TIM8_Init(void);
static void MX_TIM4_Init(void);
static void MX_ADC2_Init(void);
static void MX_TIM1_Init(void);
/* USER CODE BEGIN 0 */
void refri_init(void){
	HAL_GPIO_TogglePin(GPIOA, GPIO_PIN_2);
	TIM3->CCR4=100 - P_Controller_Init(pc);
	HAL_Delay(500);
	TIM8->CCR3=100 - P_Controller_Init(pc);
	HAL_Delay(500);
	TIM8->CCR2=100 - P_Controller_Init(pc);
	HAL_Delay(500);
}


/* USER CODE END 0 */

/**
  * @brief  The application entry point.
  * @retval int
  */
int main(void)
{

  /* MPU Configuration--------------------------------------------------------*/
  MPU_Config();

  /* MCU Configuration--------------------------------------------------------*/

  /* Reset of all peripherals, Initializes the Flash interface and the Systick. */
  HAL_Init();

  /* Configure the system clock */
  SystemClock_Config();

  /* Initialize all configured peripherals */
  MX_GPIO_Init();
  MX_DMA_Init();
  MX_ADC1_Init();
  MX_CAN1_Init();
  MX_CAN2_Init();
  MX_TIM3_Init();
  MX_TIM8_Init();
  MX_TIM4_Init();
  MX_ADC2_Init();
  MX_TIM1_Init();
  /* USER CODE BEGIN 2 */

   CAN1_FILTER_INIT(&canfil);												//CAN 1 Filter
   CAN2_FILTER_INIT(&canfil2);											//CAN 2 Filter

   CAN1_CONFIG_INIT(canfil, hcan1);										//CAN 1 Configuration - Initialization
   CAN2_CONFIG_INIT(canfil2, hcan2);										//CAN 2 Configuration - Initialization


  HAL_ADC_Start_DMA(&hadc1,(uint32_t*) adc_buffer, 2);
  HAL_TIM_Base_Start_IT(&htim4);
  HAL_TIM_PWM_Start(&htim3, TIM_CHANNEL_4);
  HAL_TIM_PWM_Start(&htim8, TIM_CHANNEL_3);
  HAL_TIM_PWM_Start(&htim8, TIM_CHANNEL_2);
  HAL_TIM_PWM_Start(&htim1, TIM_CHANNEL_1);
  refri_init();

  /* USER CODE END 2 */

  /* Infinite loop */
  /* USER CODE BEGIN WHILE */
  while (1)
  {
    /* USER CODE END WHILE */

    /* USER CODE BEGIN 3 */
  }
  /* USER CODE END 3 */
}

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
/* USER CODE BEGIN 4 */
void HAL_ADC_ConvCpltCallback(ADC_HandleTypeDef *hadc){
	   	  Susp_R_R[0] = adc_buffer[0];
	   	applyLowPassFilter(Susp_R_R);
	   	  Susp_R_L[0] = adc_buffer[1];
	   	applyLowPassFilter(Susp_R_L);
  }

void HAL_CAN_RxFifo0MsgPendingCallback(CAN_HandleTypeDef *hcan)
 {
		//Lectura del missatge rebut
	   if(HAL_CAN_GetRxMessage(hcan, CAN_RX_FIFO0, &RxHeader, RxData) != HAL_OK) Error_Handler();

	    switch(RxHeader.StdId){
	      	case(ACCU_TEMP):
	      			Temperature_Accu=((RxData[2]<<8)+RxData[3])/10;
	        }
	   }


void HAL_CAN_RxFifo1MsgPendingCallback(CAN_HandleTypeDef *hcan)
 {
	   if(HAL_CAN_GetRxMessage(hcan, CAN_RX_FIFO1, &RxHeader, RxData) != HAL_OK) Error_Handler();

	   switch(RxHeader.StdId){
	   	 		   	   case(ETAS_SYNC):
							message_cantx_RECU_Keep_Alive(hcan2, Keep_Alive, TxData, TxHeader);
	   	 					message_cantx_RECU_Data(hcan2, Susp_R_R[0], Susp_R_L[0], TxData, TxHeader);
	   	 					TSMS=HAL_GPIO_ReadPin(GPIOB, GPIO_PIN_2);
	   	 					TS_Right=HAL_GPIO_ReadPin(GPIOE, GPIO_PIN_7);
	   	 					TS_Left=HAL_GPIO_ReadPin(GPIOE, GPIO_PIN_8);
	   	 					HV_Box=HAL_GPIO_ReadPin(GPIOE, GPIO_PIN_9);
	   	 					HVD=HAL_GPIO_ReadPin(GPIOE, GPIO_PIN_10);
	   	 		   	   	   	message_cantx_RECU_SDC(hcan2,TSMS ,TS_Right ,TS_Left , HV_Box, HVD, TxData, TxHeader);
	   	 			  		Keep_Alive++;
	   	 			   break;
	   	 		   	   case(DASH_COOLING):
	   	 		     	   Refri_Accu = RxData[0] & 0b00000011;
	   	 		     	   Refri_Inverters = (RxData[0] & 0b00001100)>>2;
	   	 		     	   Refri_Motors = (RxData[0] & 0b00110000)>>4;
	   	 		       break;
	   	 		   	   case(INVERTER_L_DATA):
	   	 			       Inverter_L_Temp = ((RxData[0]<<8)+RxData[1])*0.01f;//100º offset(conversion by main ecu)
	   	 		       	   Motor_L_Temp = ((RxData[2]<<8)+RxData[3])*0.01f;
	   	 		   	   break;
	   	 		   	case(INVERTER_R_DATA):
							Inverter_R_Temp = ((RxData[0]<<8)+RxData[1])*0.01f;//100º offset(conversion by main ecu)
			   	 		    Motor_R_Temp = ((RxData[2]<<8)+RxData[3])*0.01f;
	   	 		   	       break;
	   	 		    case(BRAKELIGHT):
	   	 		    		Brakelight=RxData[0];
	   	 		    		if(Brakelight==1){
	   	 		    			HAL_GPIO_WritePin(GPIOA, GPIO_PIN_1, 1);
	   	 		    			HAL_GPIO_WritePin(GPIOA, GPIO_PIN_2, 1);
	   	 		    			HAL_GPIO_WritePin(GPIOA, GPIO_PIN_3, 1);
	   	 		    			HAL_GPIO_WritePin(GPIOA, GPIO_PIN_4, 1);
	   	 		    		}
	   	 		    		else{
	   	 		    			HAL_GPIO_WritePin(GPIOA, GPIO_PIN_1, 0);
	   	 		    			HAL_GPIO_WritePin(GPIOA, GPIO_PIN_2, 0);
	   	 		    			HAL_GPIO_WritePin(GPIOA, GPIO_PIN_3, 0);
	   	 		    			HAL_GPIO_WritePin(GPIOA, GPIO_PIN_4, 0);
	   	 		    		}

	   	 			   	    break;
	   	 		   	   }
 }
void HAL_TIM_PeriodElapsedCallback(TIM_HandleTypeDef *htim)
{
  // Check which version of the timer triggered this callback and toggle LED
  if (htim == &htim4)
  {
	if(Inverter_L_Temp>=Inverter_R_Temp){
		Inverter_Highest_Temp=Inverter_L_Temp;
	}
	else{
		Inverter_Highest_Temp=Inverter_R_Temp;
	}

	if(Inverter_L_Temp>=Inverter_R_Temp){
		Motor_Highest_Temp=Motor_L_Temp;
	}
	else{
		Motor_Highest_Temp=Motor_R_Temp;
	}

    duty_accu = P_Controller_Update(pc, Temperature_Accu, Refri_Accu, 0);
	TIM3->CCR4 = 100 - duty_accu;

    duty_motors = P_Controller_Update(pc, Motor_Highest_Temp, Refri_Motors, 1);
    TIM1->CCR1 = 100 - duty_motors;

    duty_inverters = P_Controller_Update(pc, Inverter_Highest_Temp, Refri_Inverters, 2);
    TIM8->CCR2 = 100 - duty_inverters;
  }
}
/* USER CODE END 4 */

 /* MPU Configuration */

void MPU_Config(void)
{
  MPU_Region_InitTypeDef MPU_InitStruct = {0};

  /* Disables the MPU */
  HAL_MPU_Disable();

  /** Initializes and configures the Region and the memory to be protected
  */
  MPU_InitStruct.Enable = MPU_REGION_ENABLE;
  MPU_InitStruct.Number = MPU_REGION_NUMBER0;
  MPU_InitStruct.BaseAddress = 0x0;
  MPU_InitStruct.Size = MPU_REGION_SIZE_4GB;
  MPU_InitStruct.SubRegionDisable = 0x87;
  MPU_InitStruct.TypeExtField = MPU_TEX_LEVEL0;
  MPU_InitStruct.AccessPermission = MPU_REGION_NO_ACCESS;
  MPU_InitStruct.DisableExec = MPU_INSTRUCTION_ACCESS_DISABLE;
  MPU_InitStruct.IsShareable = MPU_ACCESS_SHAREABLE;
  MPU_InitStruct.IsCacheable = MPU_ACCESS_NOT_CACHEABLE;
  MPU_InitStruct.IsBufferable = MPU_ACCESS_NOT_BUFFERABLE;

  HAL_MPU_ConfigRegion(&MPU_InitStruct);
  /* Enables the MPU */
  HAL_MPU_Enable(MPU_PRIVILEGED_DEFAULT);

}

/**
  * @brief  This function is executed in case of error occurrence.
  * @retval None
  */
void Error_Handler(void)
{
  /* USER CODE BEGIN Error_Handler_Debug */
  /* User can add his own implementation to report the HAL error return state */
  __disable_irq();
  while (1)
  {
  }
  /* USER CODE END Error_Handler_Debug */
}

#ifdef  USE_FULL_ASSERT
/**
  * @brief  Reports the name of the source file and the source line number
  *         where the assert_param error has occurred.
  * @param  file: pointer to the source file name
  * @param  line: assert_param error line source number
  * @retval None
  */
void assert_failed(uint8_t *file, uint32_t line)
{
  /* USER CODE BEGIN 6 */
  /* User can add his own implementation to report the file name and line number,
     ex: printf("Wrong parameters value: file %s on line %d\r\n", file, line) */
  /* USER CODE END 6 */
}
#endif /* USE_FULL_ASSERT */

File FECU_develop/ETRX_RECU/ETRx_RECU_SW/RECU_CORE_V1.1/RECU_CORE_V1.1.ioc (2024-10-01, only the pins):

Mcu.UserName=STM32F777VITx
PA1.Signal=GPIO_Output
PA2.Signal=GPIO_Output
PA3.Signal=GPIO_Output
PA4.Signal=GPIO_Output
PA8.Signal=S_TIM1_CH1
PB12.Signal=CAN2_RX
PB13.Signal=CAN2_TX
PB2.GPIO_Label=TSMS_TSMP
PB2.Signal=GPIO_Input
PC2.GPIO_Label=Susp_R_L
PC2.Signal=ADCx_IN12
PC3.GPIO_Label=Susp_R_R
PC3.Signal=ADCx_IN13
PC7.GPIO_Label=MOTOR_PWM
PC7.Signal=S_TIM8_CH2
PC9.GPIO_Label=ACCU_PWM
PC9.Signal=S_TIM3_CH4
PD0.Signal=CAN1_RX
PD1.Signal=CAN1_TX
PE10.GPIO_Label=HVD
PE10.Signal=GPIO_Input
PE7.GPIO_Label=Right_TS
PE7.Signal=GPIO_Input
PE8.GPIO_Label=Left_TS
PE8.Signal=GPIO_Input
PE9.GPIO_Label=HVBox
PE9.Signal=GPIO_Input

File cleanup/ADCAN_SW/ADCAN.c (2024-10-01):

/* *************************************************************************************************
**  File Name    : ADCAN.c
**  Description  : ADC conversion (microcontroller PIC18F2685) and CAN communication (MCP2561) with 
               multiple analog sensors (refer to Sensorics design) 
** ************************************************************************************************/

#include "ADCAN.h"
#include "ADCAN_vars.c"
#include "ADCAN_funs.c"

void main()
{
   //configuracio inicial programa
   Initial_Config(); //configuracio inicial del micro
   delay_ms(5);

   enable_interrupts(INT_TIMER2);
   enable_interrupts(GLOBAL);

   setup_timer_2(T2_DIV_BY_4,250,5); //overflow cada 1.0 ms

   delay_ms(3);

   enable_interrupts(int_canrx0);  

   while (true)
   {
      output_high(LED1); //led comprovacio comunicacio del micro

      if (RXB0CON.RXFUL == 1)
      {
         RXB0CON.RXFUL = 0;      // si no es gestionen els missatges
         //CANFLAG0=1;           // si es gestionen els missatges
      }
      if (RXB1CON.RXFUL == 1)
      {
         RXB1CON.RXFUL = 0;      // si no es gestionen els missatges
         //CANFLAG1=1;           // si es gestionen els missatges
      }

      // CAN SINCRONISM
      if (CAN_flag == 1)         //quan CAN_flag s'hagi activat ...
      {
         CAN_flag = 0;           //reinicia variable
         contCAN++;              //comptador de CAN_flag per enviar alive

         if ( not_first_message == 1 )
         {  
            // SEND ALIVE
            if (contCAN >= 4)   //quan CAN_flag s'hagi activat 4 vegades ...
            {
               send_alive(0xB0); //enviar senyal per indicar que el node no esta penjat
            }  

            send_data (0x85,8,APPS2,APPS1,SteeringSensor,BrakeSensor); //envia dades sensors corresponents per CAN
            send_data (0x86,4,SUSPFL,SUSPFR,0,0); //envia dades sensors corresponents per CAN

         } // END if (not_first_message == 1)         

      not_first_message = 1;      //variable per no enviar les dades quan el primer CAN_flag

      } // END CAN_flag


      if ( read_ADC_flag>0 ) //cada 1ms
      {    

         enable_interrupts(INT_TIMER2); //reinicia timer2
         read_ADC_flag = 0;

         //es llegeixen les dades de cada sensor cada 1 ms, cada 8 dades es sumen en la variable sensor_sum (s'esta fent una funcio)
         
         // APP1
         set_adc_channel(0);
         delay_us(20);
         //SUMA = read_adc();
         //APPS1_sum += SUMA;
         APPS1 = read_adc();

         // APP2
         set_adc_channel(1);
         delay_us(20);
         //SUMA = read_adc();
         //APPS2_sum += SUMA;
         APPS2 = read_adc();

         // Brake           
         set_adc_channel(2);
         delay_us(20);
         //SUMA = read_adc();
         //BrakeS_sum += SUMA;
         BrakeSensor = read_adc();

         // Steering
         set_adc_channel(3);
         delay_us(20);
         //SUMA = read_adc();        
         //Steering_sum += SUMA;
         SteeringSensor = read_adc();

         // Spring FR
         set_adc_channel(10);
         delay_us(20);
         //SUMA = read_adc();
         //SpringFR_sum += SUMA;
         SUSPFL = read_adc();

         // Spring FL 
         set_adc_channel(8);
         delay_us(20);
         //SUMA = read_adc();
         //SpringFL_sum += SUMA;
         SUSPFR = read_adc();

         output_high(LED2); //led comprovacio conversió ADC 


/*         if ( mean_filter_flag < 8 )
         {
            enable_interrupts(INT_TIMER2);
         }
         else //cada 8 ms
         {
            enable_interrupts(INT_TIMER2);
            mean_filter_flag = 0;

            //filtre per cada senyal (s'esta fent una funcio)   
            APPS1_sum = APPS1_sum >> 3;           
            APPS1 = ((APPS1_sum<<8)&0xFF00)+((APPS1_sum>>8)&0x00FF);            

            APPS2_sum = APPS2_sum >> 3;            
            APPS2 = ((APPS2_sum<<8)&0xFF00)+((APPS2_sum>>8)&0x00FF);               

            BrakeS_sum = BrakeS_sum >> 3;
            BrakeSensor = ((BrakeS_sum<<8)&0xFF00)+((BrakeS_sum>>8)&0x00FF);            

            Steering_sum = Steering_sum >> 3;           
            SteeringSensor = ((Steering_sum<<8)&0xFF00)+((Steering_sum>>8)&0x00FF);  

            SpringFR_sum = SpringFR_sum >> 3;
            SUSPFR = ((SpringFR_sum<<8)&0xFF00)+((SpringFR_sum>>8)&0x00FF);            

            SpringFL_sum = SpringFL_sum >> 3;
            SUSPFL = ((SpringFL_sum<<8)&0xFF00)+((SpringFL_sum>>8)&0x00FF);

            //reinicialitzacio variables sensor_sum (s'esta fent una funcio)
            APPS1_sum = 0;
            APPS2_sum = 0;
            BrakeS_sum = 0;
            Steering_sum = 0;
            SpringFR_sum = 0;
            SpringFL_sum = 0;

         } */
      } // END if (read_adc_flag >0)
   } // END while(1)
} // END Main

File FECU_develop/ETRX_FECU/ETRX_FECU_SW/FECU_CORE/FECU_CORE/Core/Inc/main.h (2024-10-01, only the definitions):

#define SteeringSensor_Pin GPIO_PIN_1
#define SteeringSensor_GPIO_Port GPIOC
#define SUSP_F_R_Pin GPIO_PIN_2
#define SUSP_F_R_GPIO_Port GPIOC
#define Susp_F_L_Pin GPIO_PIN_3
#define Susp_F_L_GPIO_Port GPIOC
#define APPS1_Pin GPIO_PIN_0
#define APPS1_GPIO_Port GPIOA
#define APPS2_Pin GPIO_PIN_1
#define APPS2_GPIO_Port GPIOA
#define BrakePedal_Pin GPIO_PIN_2
#define BrakePedal_GPIO_Port GPIOA
#define PitotSensor_Pin GPIO_PIN_1
#define PitotSensor_GPIO_Port GPIOB
#define SDC_SETAS_Pin GPIO_PIN_7
#define SDC_SETAS_GPIO_Port GPIOE
#define SDC_BOTS_Pin GPIO_PIN_8
#define SDC_BOTS_GPIO_Port GPIOE
#define SDC_BSPD_Intertia_Pin GPIO_PIN_9
#define SDC_BSPD_Intertia_GPIO_Port GPIOE

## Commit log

2022-02-05 Initial commit ADCAN
    [ADCAN.PcbDoc, ADCAN.PrjPCB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]
2023-09-27 Shield project
    Saving ADCAN in the ADCAN Legacy branch. Current shield project in main branch
    [ADCAN.PcbDoc, ADCAN.PrjPCB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]
2024-10-01 Antics i shield
    [ADCAN.GBL, ADCAN.GBO, ADCAN.GBP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]

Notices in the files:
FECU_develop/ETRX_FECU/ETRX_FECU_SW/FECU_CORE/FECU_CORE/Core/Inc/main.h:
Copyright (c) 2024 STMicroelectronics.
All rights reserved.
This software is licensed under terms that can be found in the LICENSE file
